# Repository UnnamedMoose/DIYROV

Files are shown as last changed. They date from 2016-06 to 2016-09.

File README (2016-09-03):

This is a README file for a home-made Remotely Operated Vehicle (ROV).
Please see Documentation/manual.pdf for detailed information about this project.

To start building your own ROV, simply checkout this repository and follow the instructions
in Documentation/manual.pdf. The individual folders of this repo contain:

- CAD - CAD files of the robot, including overview technical drawings in a pdf format.
	An Excel spreadsheet with basic design calculations is also provided. All of
	the CAD files are in Autodesk Inventor format, but an exchange file ROVassembly.stp
	has been included too. This may be imported into any CAD program (tested
	with SolidWorks 2015 Student Edition)
- Documentation - includes a report summarising the project and giving a description
	of how it all works. It gives instructions and practical tips on how to manufacture
	the ROV.
- Software
	+ controlInterface - contains Python files used to run the PC client that
		allows the ROV to be controlled
	+ HardwareInterfaces - includes custom Arduino libraries used to control
		various elements of functionality of the vehicle
	+ ROVMain - holds the main Arduino sketch that runs on the micro-controller
		on-board of the ROV
- BlockDiagrams - block diagrams of the ROV system and its various subsystem. These
	appear throughout Documentation/manual.pdf. The png versions of all the diagrams
	may be found in Documentation/Figures
- PCBDesigns - contains files used to produce PCB boards, organised in individual
	sub-folders (currently only motorControlBoard). Includes gerbers of the PCBs,
	which can readily be used to order the PCBs from a professional manufacturer
	or to etch them yourself.

Please see the LICENCE file for information on how this work may be used.

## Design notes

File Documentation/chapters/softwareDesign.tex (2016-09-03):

\pagestyle{chapter-fancy-style}
\chapter{Software design}

%=====================
\section{Overview}
The ROV software can be split into two distinct parts - the code present on the Arduino, which translates the operator commands to physical actions of the vehicle, as well as the shore-based computer part, which collects the user inputs and sends the corresponding commands to the Arduino. The remainder of this chapter covers both parts of the software separately. The computer part of the code is intended as cross-platform because its based on Python~2.7 and its open-source libraries. However, it has been developed and tested exclusively on Ubuntu 12 and 14.

%=====================
\section{Micro-controller}

%---------------------
\subsection{Program structure}
The Arduino only receives and executes operator commands, which means its functional flow is rather simple, as shown in the flowchart in Fig.~\ref{fig:arduinoMainLoop}. The \texttt{execute every instruction in series block} might involve arming the ESCs, sending readings of all the sensors, switching the forward LEDs on or off, and setting thrust levels and directions of all the motors.

\begin{figure}[]
\centering

\caption{Block diagram showing the flow of the Arduino \texttt{setup()} and \texttt{loop()} functions.}
\label{fig:arduinoMainLoop}
\end{figure}

%---------------------
\subsection{Hardware interfaces}
In order to interact with each piece of hardware, such as a sensor or electric motor, or in order to implement simple functionality, a special class \texttt{Module} has been implemented. This is holds fields such as \texttt{identifier} and \texttt{currentValue}, the combination of which is used to control a single aspect of the Arduino operation. For example, a~\texttt{Module} object called \texttt{refreshRate} holds the loop frequency the micro-controller operates at. Such basic objects typically get used directly in the \texttt{loop()} method and are treated as simple storage containers. For instance, at the end of each \texttt{loop()} call a new delay gets set as \texttt{delay(refreshRate.getValue());}, which allows setting the delay value using the same command protocol as used with more complex \texttt{Module}s.

Key methods of the \texttt{Module} class are the virtual \texttt{getValue()}, \texttt{setValue(int newValue)}, and \texttt{arm()} functions. Their default implementation in the \texttt{Module} class allows the user to read or set the value the object holds, for instance the refresh rate of the Arduino, or to initialise the object at the beginning of the execution.

Each of the modules gets created upon initialisation of the Arduino code and pointers to them are collected in arrays \texttt{Module* actuators[]} or \texttt{Module* sensors[]}, depending on their functionality. This arrangement allows the user to create classes derived from \texttt{Module} and overriding the functionality they execute when given or asked for a new value, at the same time allowing the same code in the main program loop to be used to interact with each object. A depiction of the currently used classes is shown in Figure \ref{fig:moduleClasses}. This approach is used primarily in the \texttt{parseInput()} method which is responsible for communication between the micro-controller and the PC or the \texttt{sendSensorReadings()} method which calls the \texttt{getValue()} function on each sensor module and encodes their readings into a string message which gets sent to the PC.

Currently implemented classes derived from \texttt{Module} are:
%
\begin{itemize}
\item \texttt{BrushlessDCMotor} - accepts negative and positive demand on the motor rps into the \texttt{setValue} function, treating negative values as reverse. Uses two assigned output pins in order to control the direction (binary digital output) and speed (PWM) of the motor via the ESC.
\item \texttt{LEDModule} - the value passed to the \texttt{setValue} method is treated as a binary switch telling the module to set the output pin either to HIGH or LOW state, thus controlling the LED.
\item \texttt{DepthSensor} - implements the \texttt{getValue()} method in order to return the current depth. Currently, this is a~\textbf{placeholder only}.
\end{itemize}

\begin{figure}[p]
\centering

\caption{Block diagram showing the class hierarchy of the \texttt{Module} classes used to control Arduino functionality.}
\label{fig:moduleClasses}
\end{figure}

%---------------------
\subsection{Communications}

The ROV communicates with the computer via a serial port using the USB connection. The process involves encoding messages into one-line strings and dumping them into the buffer for the other side to see. This imposes a need for strict formatting of the message packets, which is described in Table \ref{tab:commsEncoding}. Each message consists of a string flag denoting an action or a subsystem, for instance "forwardLED" or "sendSensorReadings", followed by an integer value. An arbitrary number of commands may be sent in any one packet although the length of the entire message is limited by the character buffer size on the Arduino.

During each loop, the micro-controller attempts to read data from the serial port. If any data is found, the \texttt{parseInput()} method gets called. This is responsible for checking whether the passed information conforms to the message encoding system. If yes, the string gets unwrapped into a series of flags and corresponding values. Certain flags do not require the value and so an arbitrary integer may be passed, typically a 1 indicating a boolean true.

Each flag is then compared to the names of the registered \texttt{Module} objects until a match has been found. The value corresponding to the flag gets then passed using the virtual \texttt{setValue(int value)}. This is implemented by each class derived from the baseline \texttt{Module} class if a special action is required when a new value gets passed. For instance, the \texttt{BrushlessDCMotor} class converts the integer throttle demand into values understood by the ESC and adjusts the PWM signal, flipping the thrust direction relay if necessary. Other modules holding simple integer or boolean values do not re-implement the \texttt{setValue} method.

\begin{table}[h]
\centering
\caption{Description of the special characters used to format string messages sent over the serial port.}
\label{tab:commsEncoding}
\begin{tabular}{@{}ll@{}}
\toprule
\textbf{Character} & \textbf{Meaning} \\ \midrule
$<$ & beginning of message to PC \\
$>$ & beginning of message to Arduino \\
, & delimiter \\
; & end of message \\
\bottomrule
\end{tabular}
\end{table}

%=====================
\section{Computer}

%---------------------
\subsection{Program structure}
The key piece of code that runs as an executable is the \texttt{ROVgui.py}. It
defines a class \texttt{rovGuiMainFrame}, which then gets executed inside~a 
wxWidgets application. The class itself is derived from a~base class, which
defines the basic functionality of the graphical user interface alone (discussed
in more detail later) but all of the code responsible for the operation of the
ROV itself is contained in \texttt{ROVgui.py}.
The class contains several timers which execute specific methods at fixed intervals,
for instance they ask the mirco-controller to send the sensor readings or pass
demands for the electric motors.
Each of the key aspects of the code will be discussed in more detail in the following
parts of this chapter.

%---------------------
\subsection{Communications}
The protocol used to communicate with the micro-controller via the serial connection
utilises the \texttt{serial} Python library. This simply opens a port and treats
it as a buffer to read and write from. All of the parsed messages adhere to the
structure used by the Arduino side, namely begin and end with specific characters
and each element is separated by a known delimiter. The following code listing
provides a minimum example showing how a known port is opened, written into and
read from.

\begin{lstlisting}[style=myPythonStyle,language=Python]
import serial
import time

BAUD_RATE = 19200
REFRESH_RATE = 100
PORT = "/dev/ttyACM0"

# open the connection
serialConnection = serial.Serial(PORT, BAUD_RATE, timeout = 2)

testMsgGood = True
try:
    serialConnection.inWaiting()
except:
    testMsgGood = False

if not serialConnection or not serialConnection.readable() or not testMsgGood:
    raise IOError("Connection is FUBAR!")

# keep looping and printing whatever we get from the serial
message = ">sendSensorReadings,1;"
while True:
	serialConnection.write(message)
    line = serialConnection.readline().replace("\n","")
    if line:
        print line
    time.sleep(1./REFRESH_RATE)
\end{lstlisting}

%---------------------
\subsection{User input}
Interface to the Xbox controller (Figure \ref{fig:xboxController}) has been
created using pyGame 1.9.1, an open-source library for game development.
The interface relies on pyGame joystick module capturing all the inputs provided
by the user via the controller as events. These are stored in a buffer and then
the main GUI function periodically calls the \texttt{parseEvents()} method implemented
in the \texttt{controller} class. This retrieves the most recent set of events,
clears the buffer, and updates the values of axes and button positions held
inside the \texttt{controller} object. From here they are accessed from the main GUI each time a new
set of input parameters gets sent to the micro-controller.
A minimum working example which captures the events and prings the current axes
positions in the terminal is provided

\begin{lstlisting}[style=myPythonStyle,language=Python]
import pygame
from pygame.locals import *

pygame.init()
clock = pygame.time.Clock()

joysticks = []
for i in range(0, pygame.joystick.get_count()):
        joysticks.append(pygame.joystick.Joystick(i))
        joysticks[-1].init()
        print "Detected joystick '",joysticks[-1].get_name(),"'"
while 1:
        clock.tick(60)
        for event in pygame.event.get():
                if event.type == QUIT:
                        print "Received event 'Quit', exiting."
                        return
                elif event.type == KEYDOWN and event.key == K_ESCAPE:
                        print "Escape key pressed, exiting."
                        return
                elif event.type == KEYDOWN:
                        print "Keydown,",event.key
                elif event.type == KEYUP:
                        print "Keyup,",event.key
                elif event.type == MOUSEMOTION:
                        print "Mouse movement detected."
                elif event.type == MOUSEBUTTONDOWN:
                        print "Mouse button",event.button,"down at",pygame.mouse.get_pos()
                elif event.type == MOUSEBUTTONUP:
                        print "Mouse button",event.button,"up at",pygame.mouse.get_pos()
                        
                elif event.type == JOYAXISMOTION:
                        print "Joystick '",joysticks[event.joy].get_name(),"' axis",event.axis,"motion."
                        if event.axis == 2:
                                print ' axis 2', event.value
                        elif event.axis == 5:
                                print ' axis 5', event.value
                elif event.type == JOYBUTTONDOWN:
                        print ("Joystick '",joysticks[event.joy].get_name(),
                            "' button",event.button,"down.")
                elif event.type == JOYBUTTONUP:
                        print "Joystick '",joysticks[event.joy].get_name(),"' button",event.button,"up."
                elif event.type == JOYHATMOTION:
                        print "Joystick '",joysticks[event.joy].get_name(),"' hat",event.hat," moved to",event.value
\end{lstlisting}

\begin{figure}[]
\begin{center}
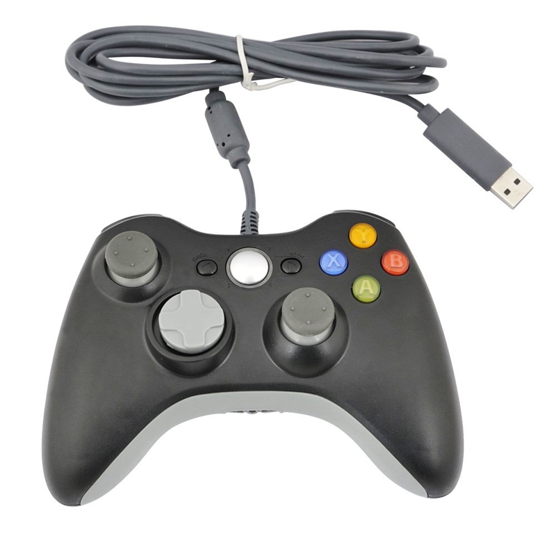
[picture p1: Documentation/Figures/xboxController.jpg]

\end{center}
\caption{USB Xbox controller used to provide control inputs to the ROV.}
\label{fig:xboxController}
\end{figure}

%---------------------
\subsection{Video acquisition}

In order to acquire imagery from the on-board USB camera, the code uses OpenCV 3.0.0-rc1,
a cross-platform, open-source digital imaging library. It is written in C++ but
provides a straightforward interface for use in Python.
In short, capturing a single frame is achieved as

\begin{lstlisting}[style=myPythonStyle,language=Python]
import cv2, wx
# create a camera
cameraID = 1
cameraCapture = cv2.VideoCapture(cameraID)
# get a picture and set up colours
ret, picture = cameraCapture.read()
height, width = picture.shape[:2]
picture = cv2.cvtColor(picture, cv2.COLOR_BGR2RGB)
# convert to wxWidgets bitmap for use inside the GUI
bmp = wx.BitmapFromBuffer(width, height, picture)
\end{lstlisting}

%---------------------
\subsection{Graphical interface}

Figure \ref{fig:GUI} shows the layout used to provide a graphical interface for
controlling the ROV. Live feed from the on-board camera is provided on the right-hand
side while the left is devoted to controlling the top-level functionality of the
vehicle. The top left-hand corner shows the thruster demand of each motor. Below,
controls are provided for the serial port connection to the Arduino, the video
feed of the camera, Xbox controller and arming of the electronic speed controllers
on board of the ROV.
There is also a pop-up Settings window which allows the user to adjust the
Arduino loop frequency, as well as frequencies for sending the control inputs,
receiving sensor readings, and camera frame rate.
The entire GUI runs on wxWidgets 2.8.12.1 and has been designed using wxFormBuilder,
both of which may be readily integrated with Python and are open-source.

\begin{figure}[]
\begin{center}
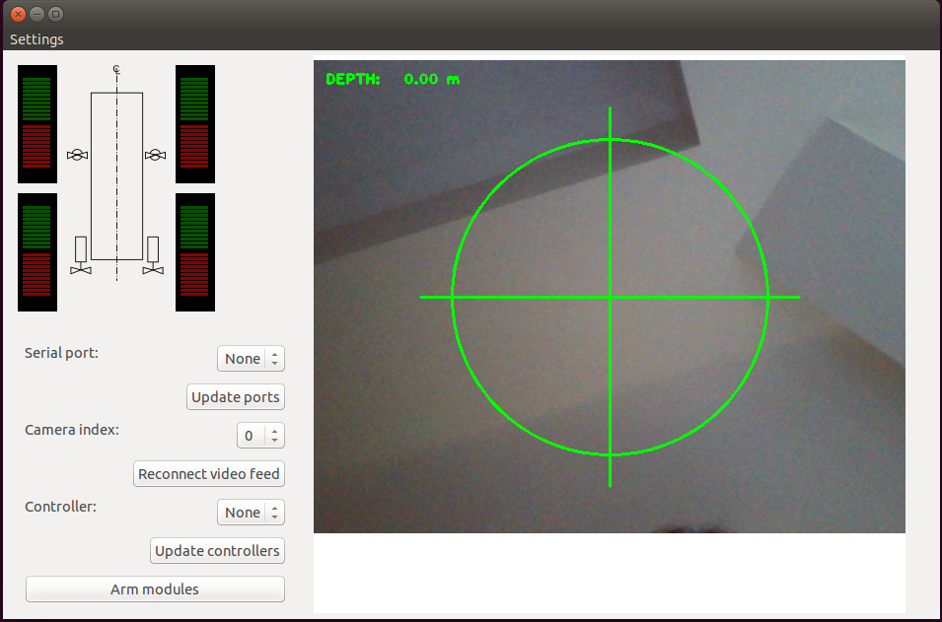
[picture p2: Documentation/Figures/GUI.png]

\end{center}
\caption{Graphical user interface (GUI) used to control the ROV from the laptop.}
\label{fig:GUI}
\end{figure}

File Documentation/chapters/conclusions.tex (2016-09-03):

\pagestyle{chapter-fancy-style}
\chapter{Conclusions}

%=====================
\section{Summary of the design}

It has been demonstrated that even within a~limited budged of less than £300 and
access only to basic tools, a~fully-functional remotely operated underwater vehicle 
can be designed, manufactured and tested.
The overall design concept using only four degrees of freedom control and employing
a compact vehicle shape has proven to provide sufficient performance that would be
expected of a low-cost sensor platform for use in shallow waters.
Several specific aspects of the design should be refined but a precious
few have also proven to be quite successful. Each of these groups will be discussed
in more detail in the subsequent parts of this chapter.

%=====================
\section{Successful design features}

Several of the chosen engineering solutions have been found to work particularly
well during the tests. These were:
%
\begin{itemize}
\item Using the on-board Arduino micro-controller to allow control of the ROV
	from a standard laptop has proven to be a very flexible and low-cost solution
\item The X-Box controller used to collect input data has been found to provide
	a robust, easy-to-use interface
\item Overall general arrangement of the vehicle has been successful and integrating
	all of the electronics into a removable internal frame allowed ease of access
	during assembly and disassembly
\item Placing the motors so that their thrust passes through the centre of gravity
	has allowed problem-free operation in the 4 DoF framework
\item Use of an external power source allowed the vehicle to be compact and
	lightweight, with the complete system fitting into an above-average sized
	rucksack and being easily transportable by hand.
\end{itemize}

%=====================
\section{Recommendations for future designs}

Despite the general success of the project, several aspects of the design could,
and a few certainly should, be improved if a next iteration or a brand new vehicle
were to be designed. These summarise the lessons learned through the development
and testing of the ROV:
%
\begin{itemize}
\item Making the aft plug removable without the use of bolts or other permanent
	connectors made it very easy to assemble the vehicle on-shore but led to
	the vehicle not being completely watertight. This is a major issue which
	could be addressed by i) using a threaded aft plug with a better seal
	ii) use of a slot-in plug secured with nuts and fitted with additional o-rings
	iii) manufacturing the pressure hull from a less compressible material (steel
	or aluminium) and desigining bespoke watertight connections
\item Removing pre-twist from the tether and making it float would make manoeuvring
	the vehicle far easier
\item Fixing the video latency issue would be necessary for operation in a real
	environment. This may require using a dedicated VGA cable, a different camera,
	or better implementation of the current software
\item At present the motors are placed in water without waterproofing which would not
	be acceptable in the long term in real environments such as seas or rivers.
	A watertight enclosure would be necessary, most likely utilising a magnetic
	coupling, to prevent corrosion of the motors.
\item Being able to redirect a time trace of control inputs and sensor readings to a file
	would make analysing the performance of the vehicle easier
\item In the present design only the internal structure was grounded, extending this
	to include all steel elements would add an important safety feature
\item Using non-linear mapping or having two sensitivity settings for the controller
	should make it easier to perform precise manoeuvres
\item Adding a sensor measuring power output of the battery would be an important
	indicator of the efficiency of the vehicle and would allow planning missions more accurately
\item At present, each of the power wires in the connector in the aft plug (section~\ref{ssection:connectorOnTheROV})
	ends with a~banana connector. Grouping the cables by the corresponding motors
	and using a~single connector for each motor
	would streamline the ROV assembly process significantly.
\item At present, the external steel frame is difficult to disassemble or even
	detach from the central hull due to the way the bolts are situated. At the
	time it was not considered crucial to allow this but having such a possibility
	would allow modifications to the design to be introduced more easily.
\item The electrical system has been significantly over-designed in most places
	in terms of current ratings. However, there are several segments with much lower
	safety factors, which effectively dictate the maximum safe power output from the battery.
	A~careful choice of suitable current ratings for each segment of the design would allow a~much
	more efficient overall system design.
\item Currently used off-the-shelf electronic speed controllers are straightforward
	to utilise but require a~large amount of wiring to operate, which takes up a~considerable
	amount of internal volume of the ROV. Using PCB-mounted variants or even controlling
	the motors directly from the Arduino by pulsing current using transistors could
	allow for a much more compact design. Ultimately, a~small PCB for a~single motor
	or a~pair of motors could be devised. The PCBs could be connected using stack-through
	connectors, thus eliminating most of the wiring used in the current design. This
	would make the system more modular, and lower-mass and thus also smaller and more agile.
\item Having the tether attach to the inspection hatch (aft plug) poses certain difficulties
	during disassembly as often multiple connectors have to be disconnected and reconnected
	just to allow a simple task to be accomplished. Moving the cable port to a stationary part
	of the hull could simplify these operations.
\item Adding controller calibration constants to the GUI settings window would make it more
	easily adjustable by the user.
\end{itemize}

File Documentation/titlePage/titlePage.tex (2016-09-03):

\begin{titlepage}

\newcommand{\HRule}{\rule{\linewidth}{0.5mm}} % Defines a new command for the horizontal lines, change thickness here

\center % Center everything on the page

%----------------------------------------------------------------------------------------
%	HEADING SECTIONS
%----------------------------------------------------------------------------------------
%\vspace*{-1cm}
%\hspace{8cm}\includegraphics[width=0.4\textwidth]{0_coreTemplate_UoSlogo_black.jpg}

\vspace*{1cm}
{\setstretch{1.5} % set bigger linespacing to make Capitals look better

%\textsc{\LARGE University of Southamtpon}\\[2.5cm] % Name of your university/college
\vspace{2.5cm}
\textsc{\huge DIY Remotely Operated Vehicle}\\[4.5cm] % Major heading

}
%----------------------------------------------------------------------------------------
%	TITLE SECTION
%----------------------------------------------------------------------------------------

\HRule \\[0.4cm]
{ \Huge \bfseries \documenttitle}\\[0.2cm] % Title of your document
\HRule \\[4.5cm]
 
%----------------------------------------------------------------------------------------
%	AUTHOR SECTION
%----------------------------------------------------------------------------------------

%\begin{minipage}{0.4\textwidth}
%\begin{flushleft} \Large
\begin{center}
\Large
\emph{Authors:}\\
Artur K. \textsc{Lidtke} \\
Aleksander A. \textsc{Lidtke}
\end{center}
%\end{flushleft}
%\end{minipage}
%~
%\begin{minipage}{0.4\textwidth}
%\begin{flushright} \Large
%\emph{Supervisors:} \\
%Prof. Stephen R. \textsc{Turnock} \\ % Supervisor's Name
%\end{flushright}
%\end{minipage}\\[4cm]

%----------------------------------------------------------------------------------------
%	DATE SECTION
%----------------------------------------------------------------------------------------

{\Large \today}\\[4cm] % Date, change the \today to a set date if you want to be precise

%----------------------------------------------------------------------------------------
%	LOGO SECTION
%----------------------------------------------------------------------------------------

%\includegraphics{Logo}\\[1cm] % Include a department/university logo - this will require the graphicx package
 
%----------------------------------------------------------------------------------------

\vfill % Fill the rest of the page with whitespace

\end{titlepage}

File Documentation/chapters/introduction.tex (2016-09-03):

\pagestyle{chapter-fancy-style}
\chapter{Introduction}

%=====================
\section{Aim}

The aim of this project was to develop a low-cost remotely operated underwater vehicle (ROV)
for operation in calm, shallow waters.
Its purpose was to allow principle physical and design challenges of building a robotic
underwater platform to be explored first-hand and to highlight possible future paths
for the development of a more refined design.
The intention of the project was not to deliver a state-of-the art vehicle and instead
focus was put on building experience and appreciation for the engineering challenges involved.
The ROV was to be manufactured, as much as possible, from easily available and affordable
off-the-shelf electronics and components. This would allow the devised solutions to
be easily reproducible by anyone with access to the most rudimentary tools and manufacturing
processes, making it easier to share the developed experiences.
The entire project, including software, CAD models, and design calculations is provided
on GitHub at \textcolor{blue}{\url{https://github.com/UnnamedMoose/DIYROV}}.

%=====================
\section{Objectives}

To achieve the specified aim, several objectives have been specified at the outset
of the project:

\begin{enumerate}
\item Create a simple software framework allowing basic electronic components to be controlled from
	a laptop via USB
\item Select a suitable means of propulsion for the ROV
\item Come up with a basic set of sensors which would make it easier to control the vehicle
	and provide basic feedback to the operator
\item Integrate the selected components into a coherent system and devise an arrangement that
	fits into a volume as small as possible
\item Design a watertight vessel to house the electronics using off-the-shelf, cheap DIY products
\item Assemble the ROV and test it in a calm environment such as a swimming pool or a~towing tank
\end{enumerate}

%=====================
\section{Subsequent parts of this document}

The following parts of this informal report will address each of the listed objectives,
and discuss them it in the context of the ultimate aim.
The intention is to convey both the engineering rationale and experience gained throughout the project,
rather than keeping the writing strictly technical. The report is accompanied by
the complete release of the necessary source code (both on-board microcontroller and shore-based computer),
CAD models of the ROV, and design calculations, all of which combined should allow
 the Reader to reproduce the process undertaken at their own leisure.

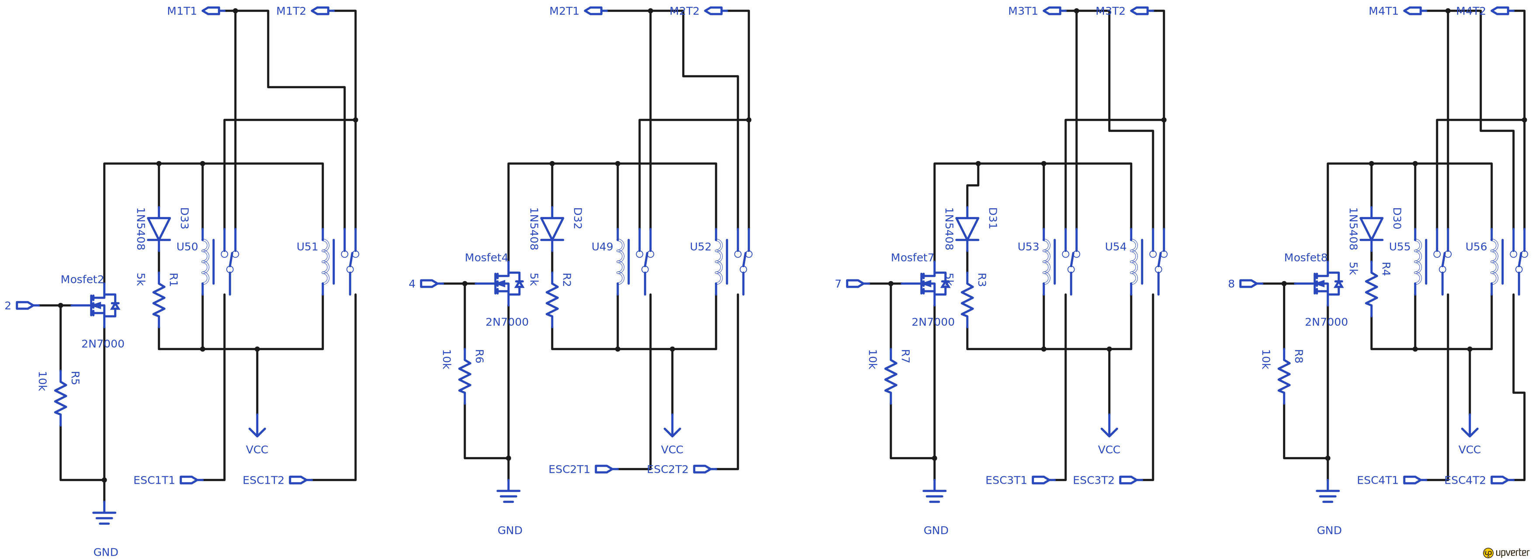
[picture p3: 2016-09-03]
PCBDesigns/BrushlessMotorControlBoard/BrushlessMotorControlBoard.png

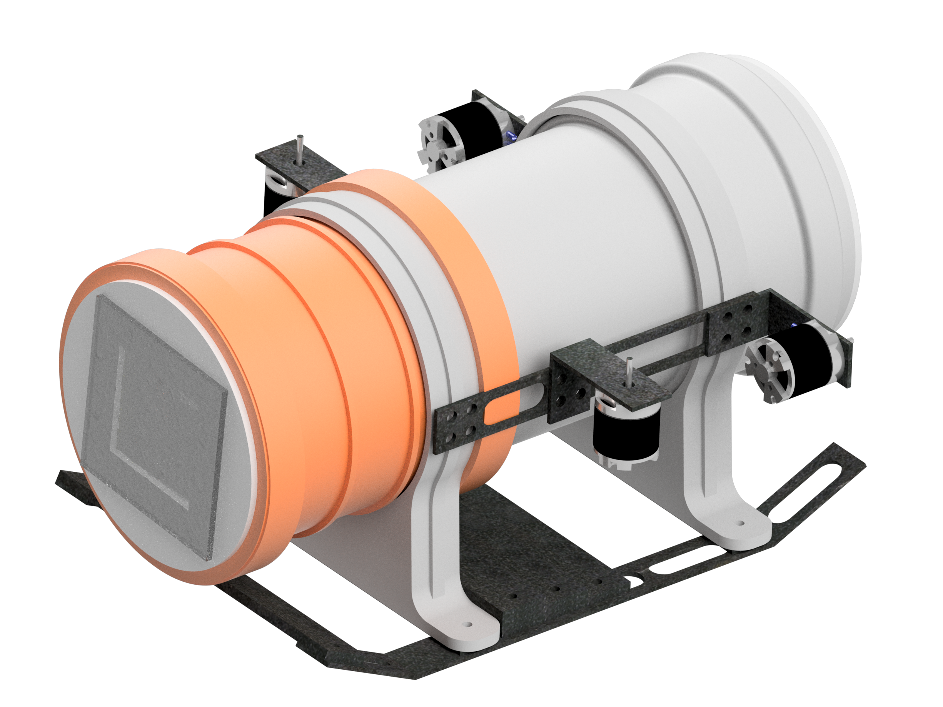
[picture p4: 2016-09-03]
Documentation/Figures/ROVrender0.png

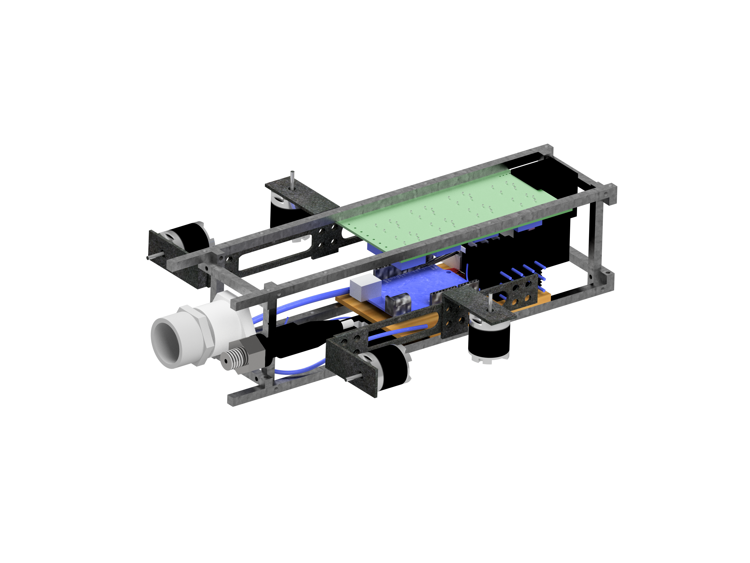
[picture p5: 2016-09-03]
Documentation/Figures/ROVrender1.png

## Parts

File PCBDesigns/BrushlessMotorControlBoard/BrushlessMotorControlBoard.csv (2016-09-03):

Reference Designator | Description | Manufacturer | Manufacturer Part Number | Suppliers | Package | Quantity | Verified Pin Names | Rms Reverse Voltage | Operating Temperature Range | Verified Pad Assignment | Verified Attributes | Average Rectified Output Current | Forward Voltage | Verified Geometry | Peak Repetitive Reverse Voltage | Mfg Package Ident | Footprint 0 Description | Imported From | Kind | Netlist | Code Jeita | Manufacturer Link | Code Jedec | Subkind | Packagedescription | Refdes | Resistance | Is Generic
D30 D31 D32 D33 | 3.0A SILICON RECTIFIER 1N5408 | Won-Top Electronics | 1N5408 |  | AXIAL | 4 | true | 700V | -65 to +125°C | true | true | 3.0A | 1.0V | true | 1000V | DO-201AD
Q1 | N-channel Enhancement Mode Field-effect Transistor | Fairchild | 2N7000 |  | TO92 | 1 | true |  |  | true | true |  |  | true |  |  | TO, Flat Index; 3 In-Line, Axial Leads; Body Dia. 4.6mm; Leads 0.48 x 0.45 mm (max) | Altium | General | @DESIGNATOR %1 %2 %3 @MODEL | SC-43 | http://www.semiconductors.philips.com/ | TO-92 | Spice Subcircuit | Plastic Single-Ended Leaded (through hole) package; 3 Leads (TO-92) | Mosfet2
Q5 | N-channel Enhancement Mode Field-effect Transistor | Fairchild | 2N7000 |  | TO92 | 1 | true |  |  | true | true |  |  | true |  |  | TO, Flat Index; 3 In-Line, Axial Leads; Body Dia. 4.6mm; Leads 0.48 x 0.45 mm (max) | Altium | General | @DESIGNATOR %1 %2 %3 @MODEL | SC-43 | http://www.semiconductors.philips.com/ | TO-92 | Spice Subcircuit | Plastic Single-Ended Leaded (through hole) package; 3 Leads (TO-92) | Mosfet4
Q6 | N-channel Enhancement Mode Field-effect Transistor | Fairchild | 2N7000 |  | TO92 | 1 | true |  |  | true | true |  |  | true |  |  | TO, Flat Index; 3 In-Line, Axial Leads; Body Dia. 4.6mm; Leads 0.48 x 0.45 mm (max) | Altium | General | @DESIGNATOR %1 %2 %3 @MODEL | SC-43 | http://www.semiconductors.philips.com/ | TO-92 | Spice Subcircuit | Plastic Single-Ended Leaded (through hole) package; 3 Leads (TO-92) | Mosfet7
Q7 | N-channel Enhancement Mode Field-effect Transistor | Fairchild | 2N7000 |  | TO92 | 1 | true |  |  | true | true |  |  | true |  |  | TO, Flat Index; 3 In-Line, Axial Leads; Body Dia. 4.6mm; Leads 0.48 x 0.45 mm (max) | Altium | General | @DESIGNATOR %1 %2 %3 @MODEL | SC-43 | http://www.semiconductors.philips.com/ | TO-92 | Spice Subcircuit | Plastic Single-Ended Leaded (through hole) package; 3 Leads (TO-92) | Mosfet8
R2 R3 R1 R4 | Generic Resistor (5k) | Generic | Resistor (5k) |  | Axial | 4 |  |  |  |  |  |  |  |  |  |  |  |  |  |  |  |  |  |  |  |  | 5k | true
R5 R6 R7 R8 | Generic Resistor (10000) | Generic | Resistor (10000) |  | Axial | 4 |  |  |  |  |  |  |  |  |  |  |  |  |  |  |  |  |  |  |  |  | 10000 | true
U49 U50 U51 U52 U53 U54 U55 U56 | Relay 5VDC | Songle Relay | JQC-3F-5VDC |  | PTH_RELAY | 8 | false |  |  | false | false |  |  | false

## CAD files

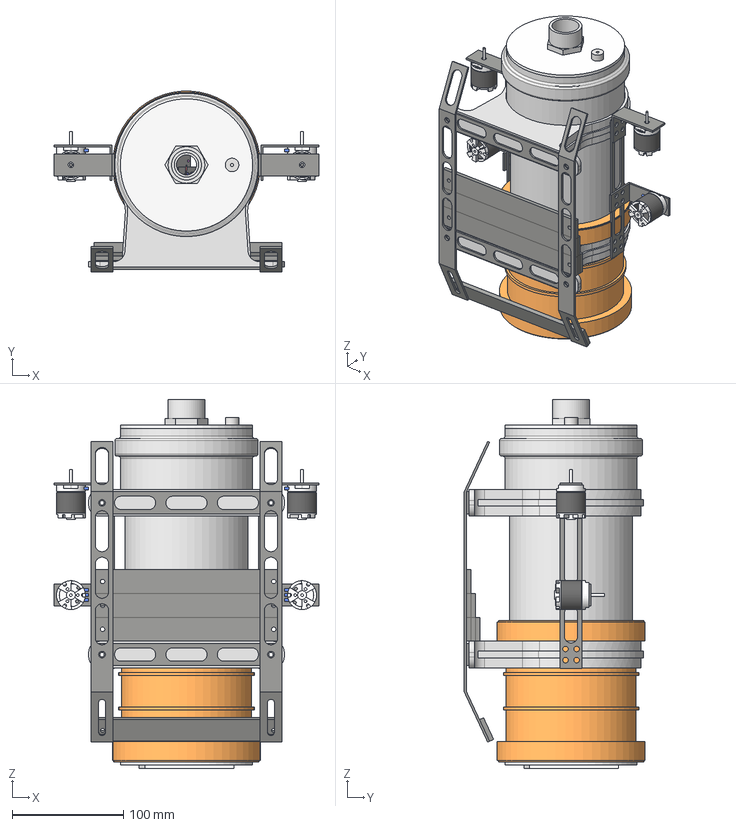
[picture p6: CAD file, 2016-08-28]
CAD/ROVassembly.stp
238.0 x 162.6 x 332.0 mm
hullPipe
longitudinal - bottom x 2
longitudinal - top x 2
transverse x 8
arduinoShelf
ArduinoUno
ESC x 4
usbRangeExtender
camera
Motor x 4
usbHubSmall
miniRelay x 8
aftPlug
PVCConnectorFemale3_4inch
frameMount x 7
plexiglassWindow
transverseClipStiffener x 2
sled x 2
30PSIPressureSensor
doubleSocketPipe
PVCConnectorMale3_4inch
socketBracket x 2
motorBracket x 4
brushlessMotorControlBoard
sideLongitudinal x 2
ROVassembly.ElectronicsHarness
CommonGNDVDD x 2
fwdPlug
ballastBarSmall
ballastBar x 6

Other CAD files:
CAD/30PSIPressureSensor.ipt
CAD/ArduinoUno.ipt
CAD/CommonGNDVDD.ipt
CAD/ESC.ipt
CAD/Motor.ipt
CAD/PVCConnectorFemale3_4inch.ipt
CAD/PVCConnectorMale3_4inch.ipt
CAD/ROVassembly.ElectronicsHarness.iam
CAD/ROVassembly.ElectronicsHarness.ipt
CAD/ROVassembly.iam
CAD/ROVassembly_external.idw
CAD/ROVassembly_internal.idw
CAD/aftPlug.ipt
CAD/arduinoShelf.ipt
CAD/ballastBar.ipt
CAD/ballastBarSmall.ipt
CAD/brushlessMotorControlBoard.ipt
CAD/camera.ipt
CAD/doubleSocketPipe.ipt
CAD/frameMount.ipt
CAD/fwdPlug.ipt
CAD/hullPipe.ipt
CAD/longitudinal - bottom.ipt
CAD/longitudinal - top.ipt
CAD/miniRelay.ipt
CAD/motorBracket.ipt
CAD/plexiglassWindow.ipt
CAD/sideLongitudinal.ipt
CAD/sled.ipt
CAD/socketBracket.ipt
CAD/transverse.ipt
CAD/transverseClipStiffener.ipt
CAD/usbHubSmall.ipt
CAD/usbRangeExtender.ipt

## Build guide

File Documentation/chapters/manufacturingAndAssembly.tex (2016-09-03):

\pagestyle{chapter-fancy-style}
\chapter{Manufacture and assembly}
%===============================================================================
\section{Architecture}
Overview of the ROV system is shown in Fig.~\ref{fig:systemBlockDiagram}, while Fig.~\ref{fig:rovGAsInternal} and Fig.~\ref{fig:rovGAsExternal} show the general dimensions of the vehicle and location of its major components. The ROV is based around an Arduino Uno R3, which is controlled and powered through its serial port connected to a~laptop. To overcome range limitations of ordinary USB cables, a~USB range extender is used, which transmits the USB signal and power over a~CAT5 cable.

The ROV houses one camera, which is operated over the same USB bus as the Arduino (the USB signal is split using an on-board USB hub). The camera field of view can be illuminated using three LED lights. Only one additional sensor, a~\unit[30]{PSI} pressure transducer, is present on board.

The ROV carries four \unit[750]{kV} brushless DC motors driven by four electronic speed controllers (ESCs). These enable forward/backward and up/down motion, as well as give control of yaw and roll. Preliminary study revealed that incorporating two additional motors, which would allow sideways motion, would require too big an investment. It would also increase the ROV displacement, thus making the vehicle larger than desired. The selected ESCs (chosen due to their low cost) can only provide thrust in one direction; a~custom printed circuit board (PCB) is used to reverse the thrust of individual motors.

The power to the motors is delivered from a~shore-based battery pack via a~three-wire power chord, which, together with the CAT5 cable, constitutes the ROV umbilical tether. The signals and power from the umbilical are delivered inside the pressure vessel via a~custom water-tight connector. In the current implementation, only the electronics sensitive to water are housed inside the pressure vessel while the brushless DC motors are exposed to water as shown in Fig.~\ref{fig:rovOverview}.

The final subsystem of the ROV, not shown in Fig.~\ref{fig:systemBlockDiagram}, is the external steel structure. It provides a~mounting point for the motors and ballast, as well as protects the ROV from hitting the bottom with the pressure vessel. The tether is also attached to this external structure, which can carry more load than the umbilical connector; this becomes important during emergency recovery, when the ROV is lifted out of the water by pulling on the tether.

The remainder of this chapter describes how the mentioned subsystems were manufactured, and how they are integrated into the system shown in Fig.~\ref{fig:systemBlockDiagram}. Components are grouped into subsystems based on their function. Thus, section~\ref{section:electronics} describes the electronics, which provide the ROV with its top-level functionality. The pressure vessel, made of PVC pipes and providing water-tight volume for the electronics, is described in section~\ref{section:pressureVessel}. The vessel is surrounded by an external structure described in section~\ref{section:externalStructure}. Lastly, the umbilical tether is described in section~\ref{section:umbilical}.

\begin{figure}[htb]
\begin{minipage}[b]{1\linewidth}
  \centering
	
\end{minipage}
\caption{The ROV system block diagram. \textcolor{cyan}{CAT5 cable} and \textcolor{red}{Three-wire power cord} constitute the umbilical tether (marked with the~pink rectangle). The black rectangle marks the extents of the pressure vessel.}
\label{fig:systemBlockDiagram}
\end{figure}

\begin{figure}[htb]
\begin{center}
	
\end{center}
\caption{External general arrangement of the current version of the ROV. Drawing not to scale, original provided in a~separate file.}
\label{fig:rovGAsExternal}
\end{figure}

\begin{figure}[htb]
\begin{center}
	
\end{center}
\caption{Internal general arrangement of the current version of the ROV. Drawing not to scale, original provided in a~separate file.}
\label{fig:rovGAsInternal}
\end{figure}

\begin{figure}[htb]
\begin{tabular}{c}
	\subfloat[CAD render]
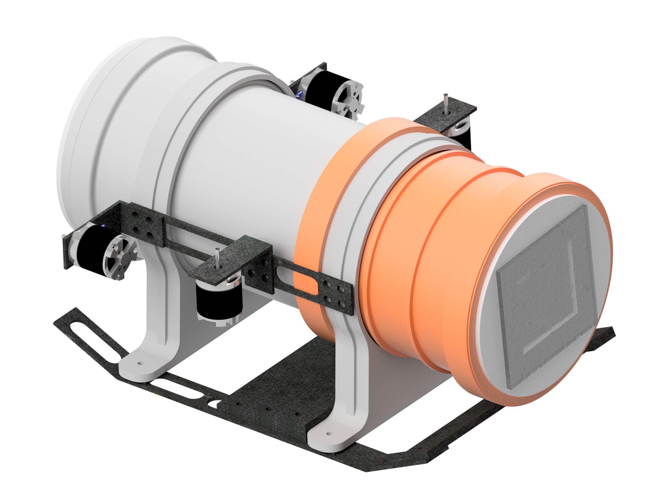
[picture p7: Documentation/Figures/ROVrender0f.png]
		{
		\label{fig:rovOverview:label:a} } \\
	\subfloat[Photo]
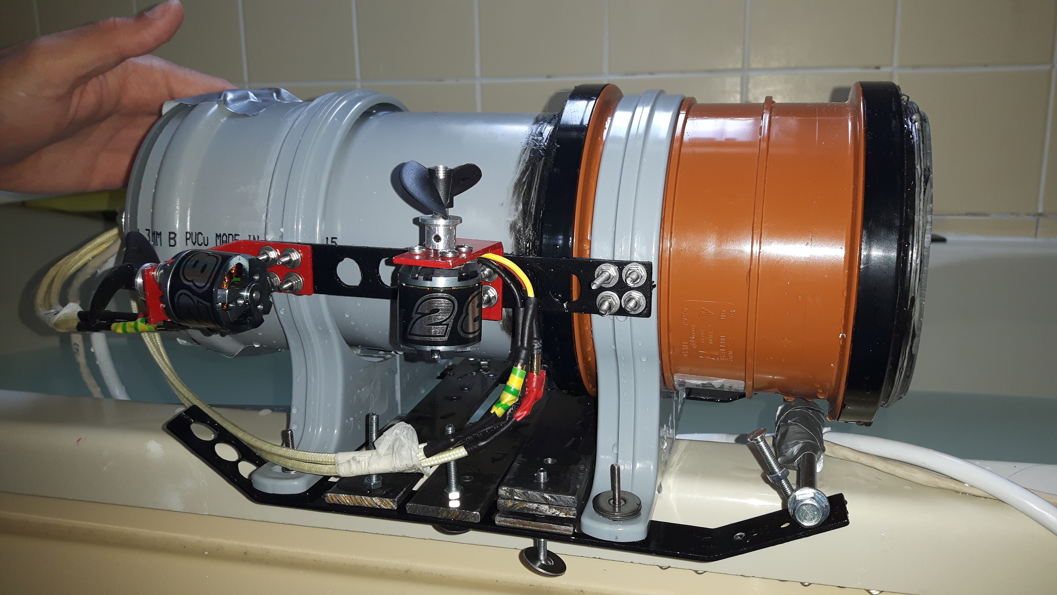
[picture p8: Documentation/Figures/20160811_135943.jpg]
		{
		\label{fig:rovOverview:label:b} } \\
\end{tabular}
\caption{Overview of the ROV.}
\label{fig:rovOverview}
\end{figure}

\clearpage % Avoid "too many unprocessed floats" error.

%===============================================================================
\section{On-board electronics}\label{section:electronics}

%-------------------------------------------------------------------------------
\subsection{Architecture and physical arrangement}
The electronics are mounted to an internal structure, which is made of \unit[4 by 4]{mm} aluminium bars. The bars are bolted together to form a~frame with a~square cross-section. The frame, with the electronics attached to it, slides into the pressure vessel as shown in Fig.~\ref{fig:electronicsSlideIn}. A~PVC plug (aft plug from section~\ref{sscetion:aftPlug}) then slides in and seals the pressure vessel. The electrical connections between the internal electronics, and the motors and the shore are routed through a~connector in the aft plug, described in section~\ref{ssection:connectorOnTheROV}.

The Arduino, USB hub and ESCs are mounted onto a~plywood bed, which bolts onto the aluminium frame. This plywood bed and the USB hub are visible in Fig.~\ref{fig:usbExtenderAndHub}. The PCB, which enables the thrust of the motors to be reversed (described in section~\ref{ssection:motorControlBoard}), is also bolted onto the frame, directly above the plywood bed as shown in Fig.~\ref{fig:simpleInternalOverview}. The camera is integrated into a~stand-alone module with three LEDs, as described in section~\ref{ssection:ledAndCamera}; this module is attached to the aluminium frame using cable ties. The USB range extender and power distribution units (described in section~\ref{ssection:powerDsitrbution}) are also attached to the internal frame using cable ties.

\begin{figure}[htb]
\begin{minipage}[b]{1\linewidth}
  \centering
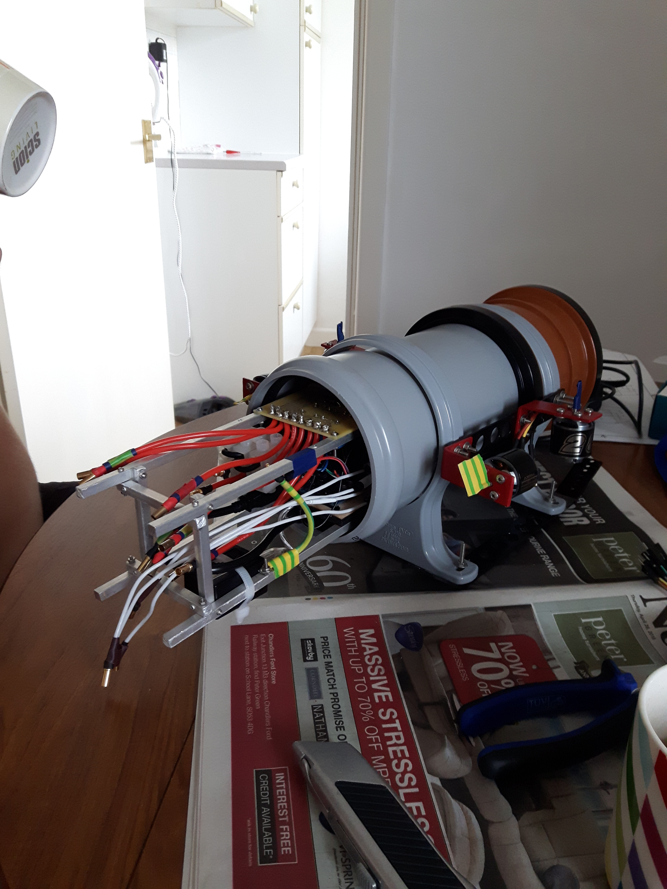
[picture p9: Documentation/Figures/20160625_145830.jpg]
	
\end{minipage}
\caption{Electronics are mounted to the internal aluminium structure, which slides into the pressure vessel.}
\label{fig:electronicsSlideIn}
\end{figure}

\begin{figure}[htb]
\begin{minipage}[b]{1\linewidth}
  \centering
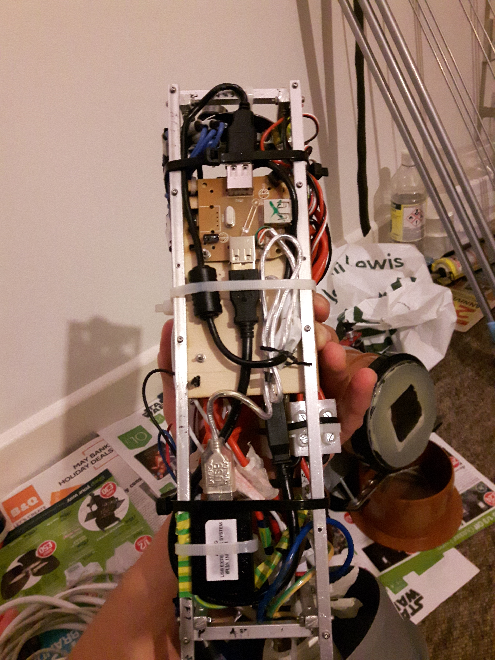
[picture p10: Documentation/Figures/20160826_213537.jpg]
	
\end{minipage}
\caption{USB range extender (black box on the bottom left of the phot) is mounted to the aluminium internal structure with a~white cable tie. The USB hub, into which Arduino and the webcam are plugged in, is bolted onto the underside of the plywood bed.}
\label{fig:usbExtenderAndHub}
\end{figure}

\begin{figure}[htb]
\begin{minipage}[b]{1\linewidth}
  \centering
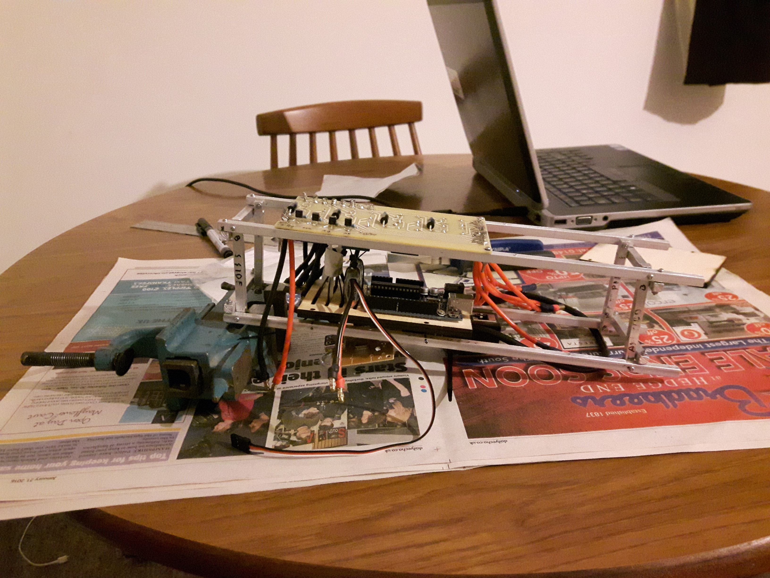
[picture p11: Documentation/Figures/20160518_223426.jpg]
	
\end{minipage}
\caption{General arrangement of the internal electronics. Only one electronic speed controller, and no LEDs and camera are mounted for clarity.}
\label{fig:simpleInternalOverview}
\end{figure}

\clearpage % Place these figures close to the text.

%-------------------------------------------------------------------------------
\subsection{Power distribution subsystem}\label{ssection:powerDsitrbution}
Block diagram of the on-board power distribution subsystem is shown in Fig.~\ref{fig:powerBlockDiagram}. The Arduino and the camera are powered directly from the USB bus delivered on board via the CAT5 cable, which forms part of the tether (c.f. section~\ref{section:umbilical}). The USB bus is changed from the CAT5 cable to a~standard USB cable using the USB range extender, and then split by the USB hub to deliver power to both the camera and the Arduino.

The pressure sensor is powered from the Arduino \unit[5]{V} pin. The LEDs are turned on by setting an Arduino pin high, which provides sufficient power for them to operate. Both the pressure sensor and the LEDs are connected to the Arduino ground, and connections to both peripherals are realised using hookup wires.

The power for the ESCs and the motor control board is delivered from the shore-based battery via the power cable, which constitutes part of the tether. Custom power distribution unit (PDU) and common ground for these five components were manufactured out of automotive cable connectors. These components are shown in Fig.~\ref{fig:commonGround}; they connect the ESCs and the motor control board in parallel.

The ground (GND) of the Arduino is connected to four ESCs. However, these connections are separate from the ones that deliver power to the ESCs (negative battery terminals). Whether the Arduino GND and and battery GND are connected via the ESCs is unknown. The motor control board connects the Arduino and battery GND, as described in section~\ref{ssection:motorControlBoard}.

Power is delivered to the ESCs and motor control board using gauge 32 wires (thick lines in Fig.~\ref{fig:powerBlockDiagram}). All other connections in Fig.~\ref{fig:powerBlockDiagram} are realised using hookup wires.

The third wire in the power cable (besides battery positive and negative terminals) is used to ground the internal structure. This is intended to protect the operators in case the battery positive terminal short-circuits to one of the internal components or the aluminium structure. The external structure is not grounded.

The shore battery pack constitutes two \unit[6]{V} batteries connected in series. These are housed inside an aluminium box, which also incorporates a~\unit[20]{mm} fuse, switches and leads that can be used to monitor the battery voltage. Disassembled battery pack is shown in Fig.~\ref{fig:batteryPack}.

\begin{figure}[htb]
\begin{minipage}[b]{1\linewidth}
  \centering
	
\end{minipage}
\caption{Block diagram of the power distribution subsystem. Power is delivered to the aft plug using the umbilical tether, which is connected to the battery pack.}
\label{fig:powerBlockDiagram}
\end{figure}

\begin{figure}[htb]
\begin{center}
\begin{tabular}{c c}
	\subfloat[Side]
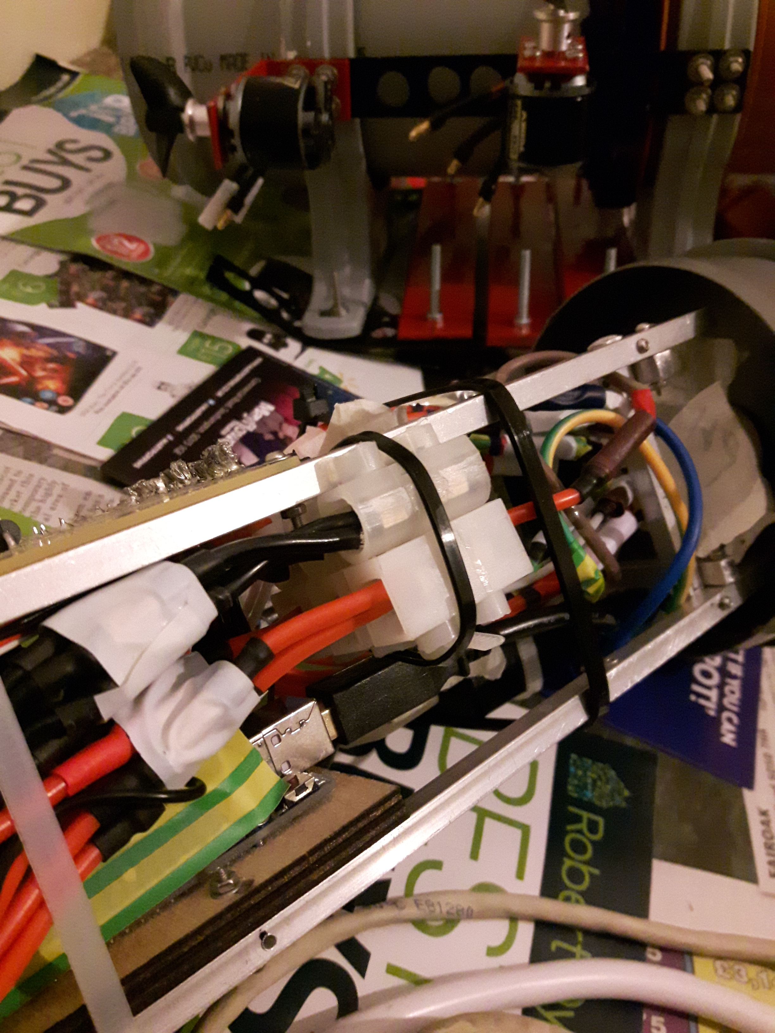
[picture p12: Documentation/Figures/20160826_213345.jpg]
		{
		\label{fig:commonGround:label:a} } &
	\subfloat[Top]
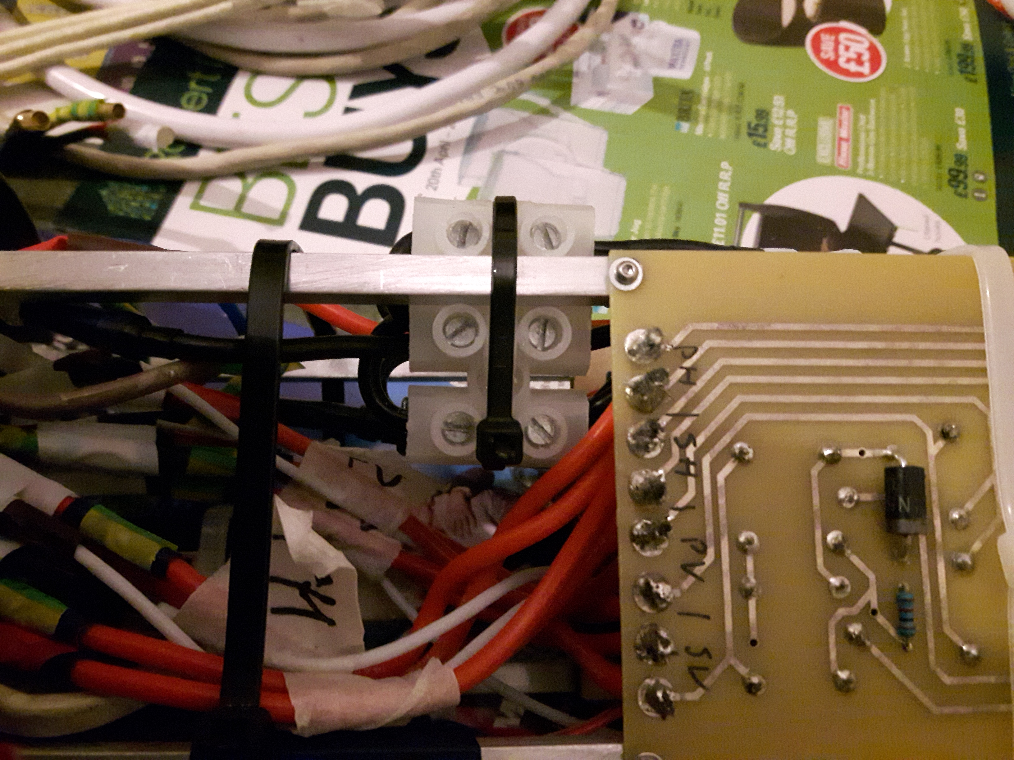
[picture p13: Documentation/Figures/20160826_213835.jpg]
		{
		\label{fig:commonGround:label:b} } \\
\end{tabular}
\end{center}
\caption{Side and top views of the common ground and common power lines made out of screw automotive cable connectors and mounted to the aluminium internal structure with cable ties.}
\label{fig:commonGround}
\end{figure}

\begin{figure}[htb]
\begin{minipage}[b]{1\linewidth}
  \centering
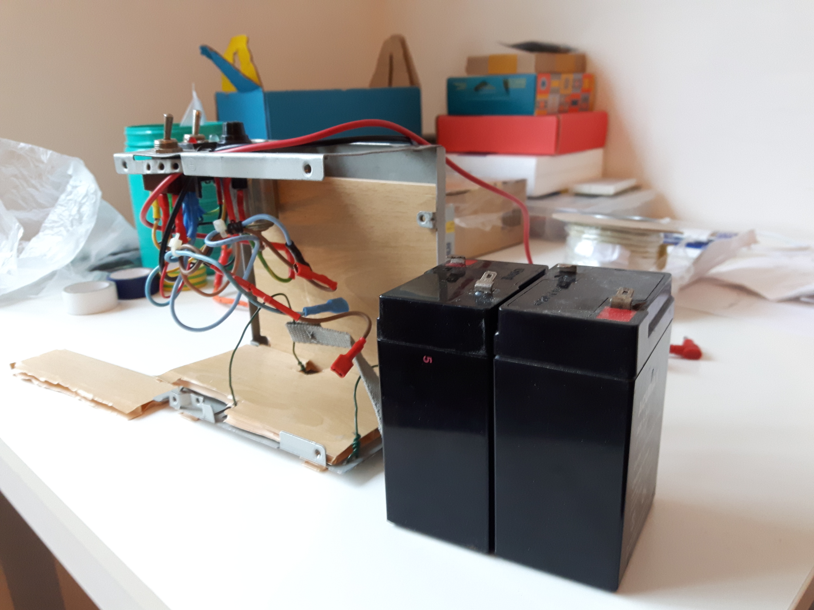
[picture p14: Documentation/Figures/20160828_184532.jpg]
	
\end{minipage}
\caption{Disassembled battery pack. One switch enables the batteries to be connected in parallel or in series (series configuration is used for the ROV project) while the other one switches the power on or off. The output of the battery pack is protected from excessive currents using a~\unit[20]{mm} fuse.}
\label{fig:batteryPack}
\end{figure}

\clearpage % Place these figures close to the text.

%-------------------------------------------------------------------------------
\subsection{Propulsion subsystem}\label{ssection:propulsionSubsystem}
Block diagram of the ROV propulsion subsystem is shown in Fig.~\ref{fig:propulsionBlockDiagram}. It is based on four brushless DC motors that are driven by four commercial, off-the-shelf electronic speed controllers. Every ESC converts a~pulse width modulation signal (PWM) from the Arduino into pulses of power delivered to every of three terminals on the brushless motor. Changing the frequency of the PWM changes the frequency of the power pulses, which changes the rotation frequency of the motor and so also its thrust. This PWM signal is delivered from the Arduino pins using hookup wires. The ESCs draw power, which is then delivered to the motors in pulses, directly from the shore-based batteries, which is described in section~\ref{ssection:powerDsitrbution}.

In order to reverse thrust of the motor, it suffices to swap two out of three signals output by the ESC. This is achieved by a~custom printed circuit board, which is described in more detail in section~\ref{ssection:motorControlBoard}. Two out of three outputs of every ESC (terminals 1 and 2 in Fig.~\ref{fig:propulsionBlockDiagram}) are routed through this board, before they are delivered to the corresponding motors using the connector in the aft plug using red wires in Fig.~\ref{fig:electronicsSlideIn}. The third signal of every ESC (terminal 3 in Fig.~\ref{fig:propulsionBlockDiagram}) circumvents the motor control board and connects to the corresponding motor only through the connector in the aft plug (white wires in Fig.~\ref{fig:electronicsSlideIn}). The commands to swap the thrust of a~given motor are issued to the motor control board via hookup wires connected to the Arduino pins.

The ESCs are mounted to the plywood bed ahead of the Arduino using cable ties (the aft-most ESC is visible in Fig.~\ref{fig:simpleInternalOverview}). The ESCs connect to the motor control board, the aft plug connector, and the motors using gauge 32 wires.

\begin{figure}[htb]
\begin{minipage}[b]{1\linewidth}
  \centering
	
\end{minipage}
\caption{Block diagram of the ROV propulsion subsystem. \textcolor{purple}{Connections from the Arduino} are realised using hookup wires. All other signals (\textcolor{red}{power}, and ESC signals \textcolor{green}{1, 2} and \textcolor{orange}{3}) are carried using gauge 32 wire.}
\label{fig:propulsionBlockDiagram}
\end{figure}

%-------------------------------------------------------------------------------
\subsection{Brushless-motor control board}\label{ssection:motorControlBoard}
As explained in section~\ref{ssection:propulsionSubsystem}, two signals from every ESC have to be swapped in order to reverse the thrust of a~motor. The schematic of the circuit, which achieves this, is shown in Fig.~\ref{fig:motorControlBoardSchematic}. Nominally, terminals 1 and 2 of every ESC (e.g. ESC1T1 and ESC1T2 for ESC no.~1) are connected to terminals 1 and 2 of the corresponding motor (e.g. M1T1 and M1T2 for motor no.~1). When a~command to reverse the thrust of a~given motor is issued by the Arduino by setting one of its pins high (e.g. pin~2 for motor no.~1), an n-type mosfet activates two switching relays. This connects terminals 1 and 2 of the ESC with terminals 2 and 1 of the motor, respectively, thus reversing the thrust. When the command pin is set low, the relays switch back to the nominal configuration and thrust is no longer reversed.

The power output of the Arduino is insufficient to activate the relays - relatively large relays, which can withstand currents output by the ESCs, have to be used. Thus, the power to the relays is delivered by the shore-based batteries. Every ESC-motor pair requires two switching relays, and every two relays have one flyback diode.

A~two-layer PCB houses the entire circuit from Fig.~\ref{fig:motorControlBoardSchematic}; its layout is shown in Fig.~\ref{fig:motorControlBoardLayout}. The motor control PCB is manufactured with 1 oz Cu and has trace widths of at least \unit[1]{mm} rated to at least \unit[2.5]{A}. The design of this board is open-source, and can be accessed in its repository at: \textcolor{blue}{\url{{www.upverter.com/AleksanderLidtke/7eccd1441d1097f8/BrushlessMotorControlBoard/}}}.

\begin{figure}[htb]
\begin{minipage}[b]{1\linewidth}
  \centering
	
\end{minipage}
\caption{Schematic of the brushless motor control PCB. The board connects terminals of ESCs to motor terminals via pairs of switching relays.}
\label{fig:motorControlBoardSchematic}
\end{figure}

\begin{figure}[htb]
\begin{minipage}[b]{1\linewidth}
  \centering
	
\end{minipage}
\caption{Layout of the brushless motor control PCB. Bottom copper marked with \textcolor{green}{green}, top with \textcolor{blue}{blue}, and component outlines with \textcolor{red}{red}. Switching relays are mounted on the top, and resistors, diodes and n-type mosfets on the bottom of the board. The PCB is actually mounted upside down in the vehicle, so that the bottom copper layer is facing the top of the ROV.}
\label{fig:motorControlBoardLayout}
\end{figure}

\clearpage % Place these figures close to the text.

%-------------------------------------------------------------------------------
\subsection{LEDs and camera}\label{ssection:ledAndCamera}
A~small, one-layer PCB, which houses three white LEDs connected in series, is mounted to a~reflective plastic surface. A~hole is drilled in the plastic, through which a~disassembled USB webcam is pointed in the direction of the LED lights. These LEDs and camera form a~stand-alone module, which is shown in Fig.~\ref{fig:forwardLED:label:a}. The module is mounted to the front of the internal aluminium frame of the ROV using cable ties, as shown in Fig.~\ref{fig:forwardLED:label:b}. A~translucent window is placed in the pressure vessel in front of the camera, which is described in section~\ref{ssection:forwardPlug}. As shown in Fig.~\ref{fig:powerBlockDiagram}, the LEDs are activated and powered directly from a~GPIO pin of the Arduino, whereas the camera is powered and operated via the USB bus.

\begin{figure}[htb]
\begin{center}
\begin{tabular}{c c}
	\subfloat[LED and camera module]
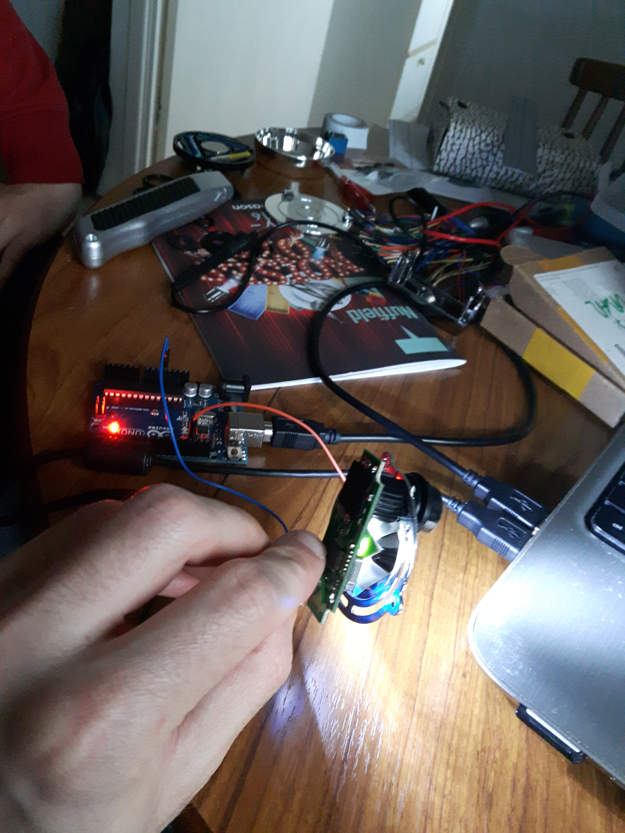
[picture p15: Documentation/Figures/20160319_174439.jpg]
		{
		\label{fig:forwardLED:label:a} } &
	\subfloat[Module mounting]
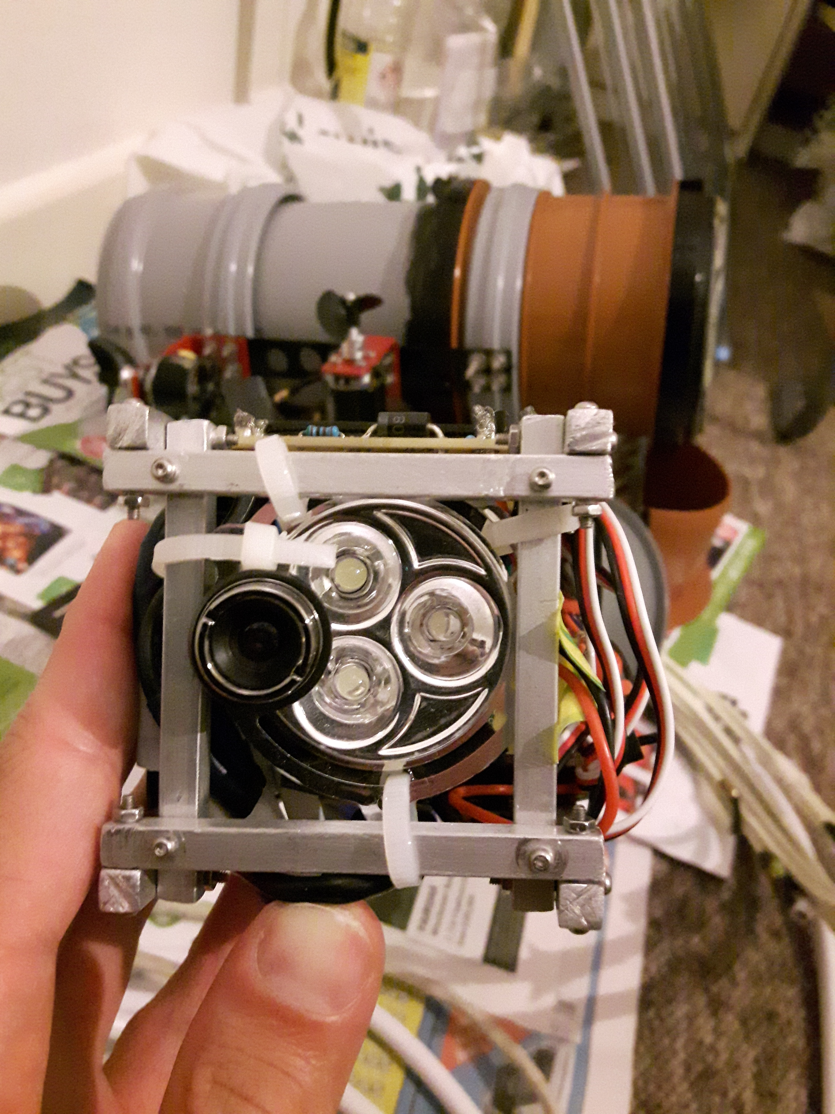
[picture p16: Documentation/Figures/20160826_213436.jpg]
		{
		\label{fig:forwardLED:label:b} } \\
\end{tabular}
\end{center}
\caption{The module, which houses the LEDs and the camera, and its mounting in the vehicle.}
\label{fig:forwardLED}
\end{figure}

%-------------------------------------------------------------------------------
\subsection{Pressure sensor}\label{ssection:pressureSensor}

A~\unit[30]{PSI} pressure transducer, depicted in Figure \ref{fig:pressureTransducer}, is mounted in the aft plug, which is a~modified PVC socket plug shown in Fig.~\ref{fig:socketPlug}. A~hole was punched in the socket plug, into which the pressure sensor was screwed in. The connection was sealed by applying PTFE tape on the thread of the pressure transducer and inserting rubber washers on either side of the socket plug. The entire assembly was then tightened using a~nut and a~washer placed on the external side of the socket plug. The inlet of the pressure sensor, brass nut and a~steel washer, under which a~rubber washer is placed, can be seen in Fig.~\ref{fig:externalSideOfTheAftPlug}. The transducer is powered from the Arduino \unit[5]{V} pin through a~hookup wire. It is connected to the Arduino GND and an analogue input pin using hookup wires as well.

\begin{figure}[htb]
\centering
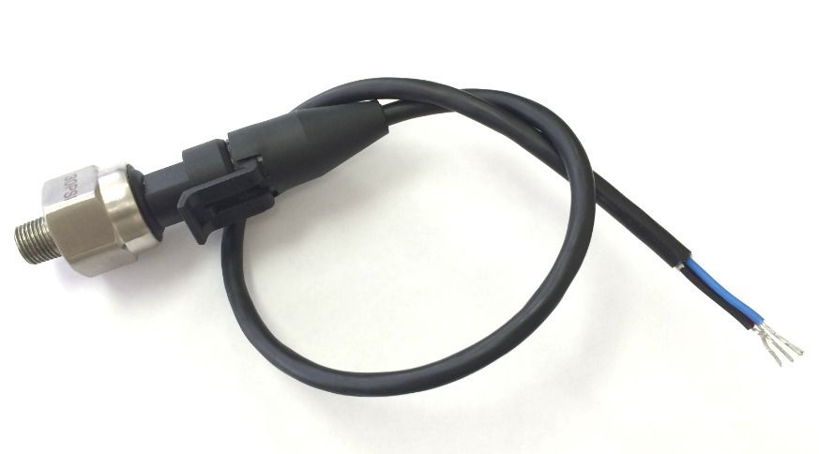
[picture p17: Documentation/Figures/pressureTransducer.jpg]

\caption{Overview of the pressure transducer.}
\label{fig:pressureTransducer}
\end{figure}

\begin{figure}[htb]
\begin{minipage}[b]{1\linewidth}
  \centering
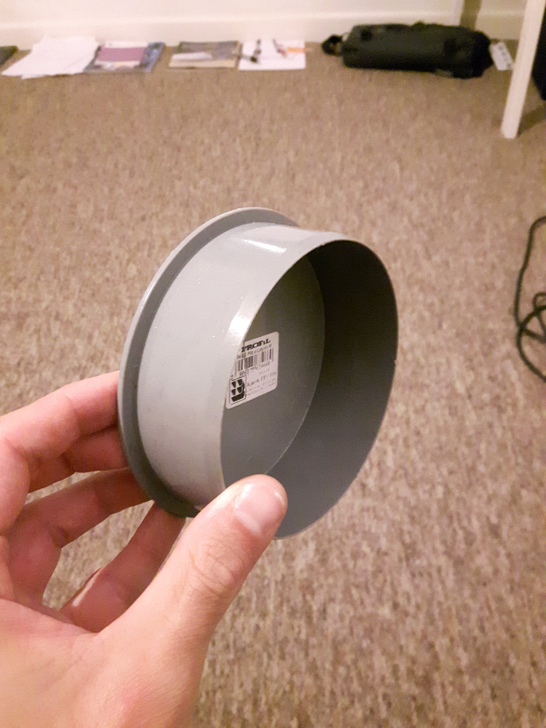
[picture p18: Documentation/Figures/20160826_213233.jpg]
	
\end{minipage}
\caption{Socket plug used to manufacture the aft and forward plug.}
\label{fig:socketPlug}
\end{figure}

%-------------------------------------------------------------------------------
\subsection{Ardunio pinout}\label{ssection:arduinoPinout}

Table \ref{tab:pinoutMain} describes all of the Arduino connections used by the ROV. Thrust direction pins are responsible for switching the relays on the motor control board via mosfet transistors, and throttle pins are connected to the ESCs directly and control motor rpm using PWM signals (see section~\ref{ssection:motorControlBoard} for details).

\begin{table}[h]
\centering
\caption{Pinout showing Arduino connections.}
\label{tab:pinoutMain}
\begin{tabular}{@{}ll@{}}
\toprule
\textbf{Pin  no.} & \textbf{Connect net} \\ \midrule
2 & Motor port horizontal - thrust direction \\
3 & Motor port horizontal - throttle \\
4 & Motor starboard horizontal - thrust direction \\
5 & Motor starboard horizontal - throttle \\
6 & Motor port vertical - throttle \\
7 & Motor port vertical - thrust direction \\
8 & Motor starboard vertical - thrust direction \\
9 & Motor starboard vertical - throttle \\
12 & Forward LED on/off \\
A0 & Pressure transducer analogue input \\
5 V & Pressure transducer VDD \\
\bottomrule
\end{tabular}
\end{table}

%===============================================================================
\section{Pressure vessel}\label{section:pressureVessel}

%-------------------------------------------------------------------------------
\subsection{Aft plug}\label{sscetion:aftPlug}
The aft plug is made of a~PVC socket plug shown in Fig.~\ref{fig:socketPlug}. Two holes were punched in it - one, into which the pressure transducer is screwed in, as described in section~\ref{ssection:pressureSensor}, and one, which houses the umbilical connector described in section~\ref{ssection:connectorOnTheROV}.

The external side of the aft plug (the wet side of the ROV), with the pressure transducer and umbilical connector mounted, is shown in Fig.~\ref{fig:externalSideOfTheAftPlug}. Its internal side is shown in Fig.~\ref{fig:internalSideOfTheAftPlug}; the body of the pressure sensor, CAT5 cable, power chord, and 12 motor wires (three signals per each of the four motors) can be seen on this side. The plug can be removed from the main pressure vessel to enable inspection and modification of the interior of the ROV. In order to ease the process and improve the water-tightness, silicone lubricant from Fig.~\ref{fig:lubricant} is applied on the aft plug before it is slid into the main pressure vessel. Once in place, the aft plug is secured using a~water-resistant duct tape.

\begin{figure}[htb]
\begin{minipage}[b]{1\linewidth}
  \centering
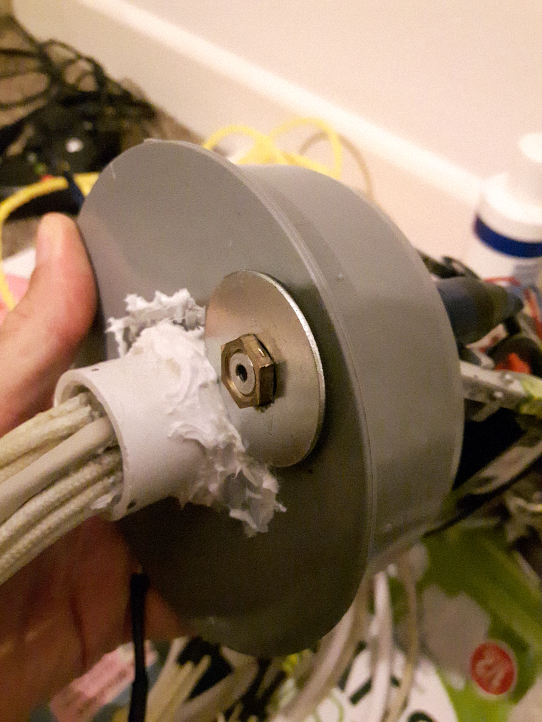
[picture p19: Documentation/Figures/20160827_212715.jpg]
	
\end{minipage}
\caption{External side of the aft plug with the pressure sensor and umbilical connector mounted.}
\label{fig:externalSideOfTheAftPlug}
\end{figure}

\begin{figure}[htb]
\begin{minipage}[b]{1\linewidth}
  \centering
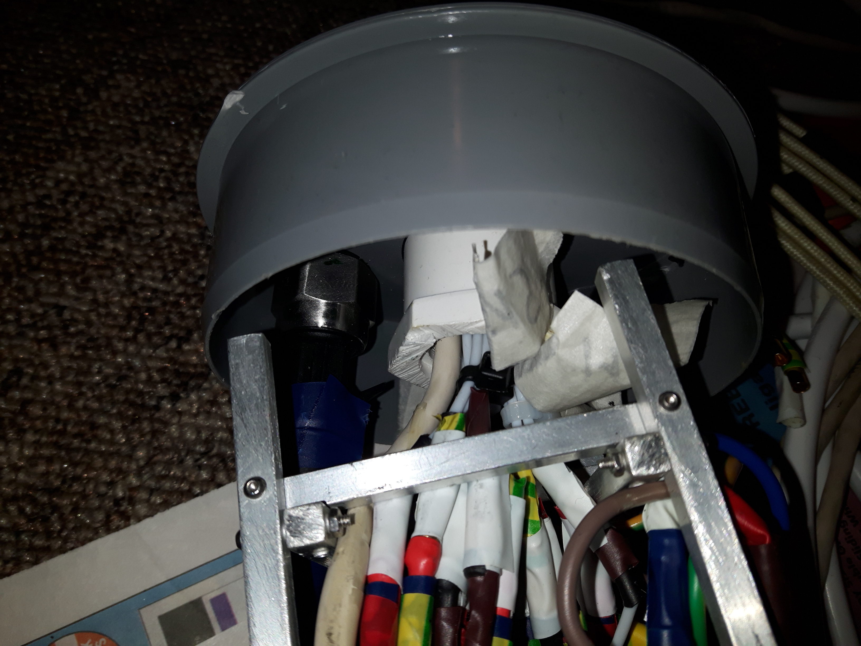
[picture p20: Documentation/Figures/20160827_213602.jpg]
	
\end{minipage}
\caption{Internal side of the aft plug with the pressure sensor and umbilical connectors mounted. The CAT5 cable is plugged into the USB range extender, and all motor wires are connected to the ESCs and the motor control board.}
\label{fig:internalSideOfTheAftPlug}
\end{figure}

\begin{figure}[htb]
\begin{minipage}[b]{1\linewidth}
  \centering
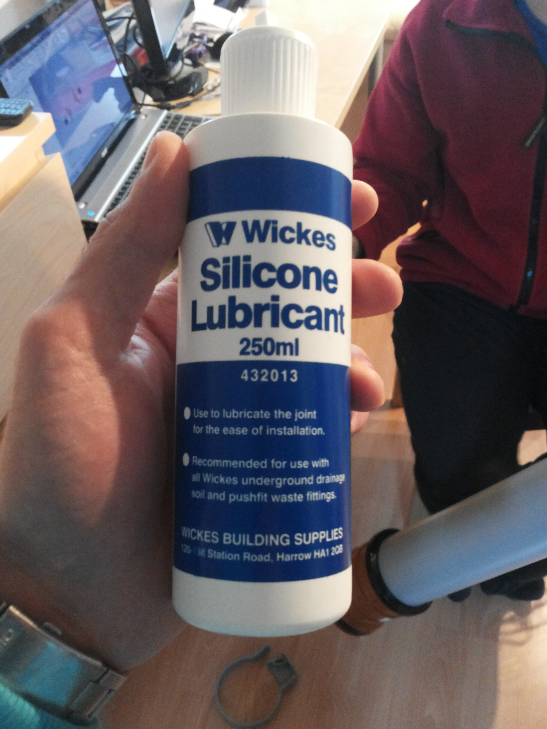
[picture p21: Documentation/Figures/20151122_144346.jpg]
	
\end{minipage}
\caption{When the aft plug is slid into the main pressure vessel, this silicone lubricant is applied onto it to ease the assembly and improve the seal.}
\label{fig:lubricant}
\end{figure}

%-------------------------------------------------------------------------------
\subsection{Forward plug}\label{ssection:forwardPlug}
The forward plug was manufactured from a~socket plug identical to the one used for manufacture of the aft plug (shown in Fig.~\ref{fig:socketPlug}). The forward plug has to enable the camera to photograph the space in front of the ROV to enable remote operation. To this end, a~hole was cut in the socket plug as shown in Fig.~\ref{fig:cuttingAHole}. A~window was cut out of a~\unit[4]{mm} thick plexiglass, which was glued onto the outer side of the socket plug using a~two-part epoxy glue. The complete forward plug is fixed in the pressure vessel using silicone; this provides both structural strength and makes the connection water-tight. The complete forward plug, mounted into the pressure vessel, can be seen in Fig.~\ref{fig:assembledPressureVessel}.

\begin{figure}[htb]
\begin{minipage}[b]{1\linewidth}
  \centering
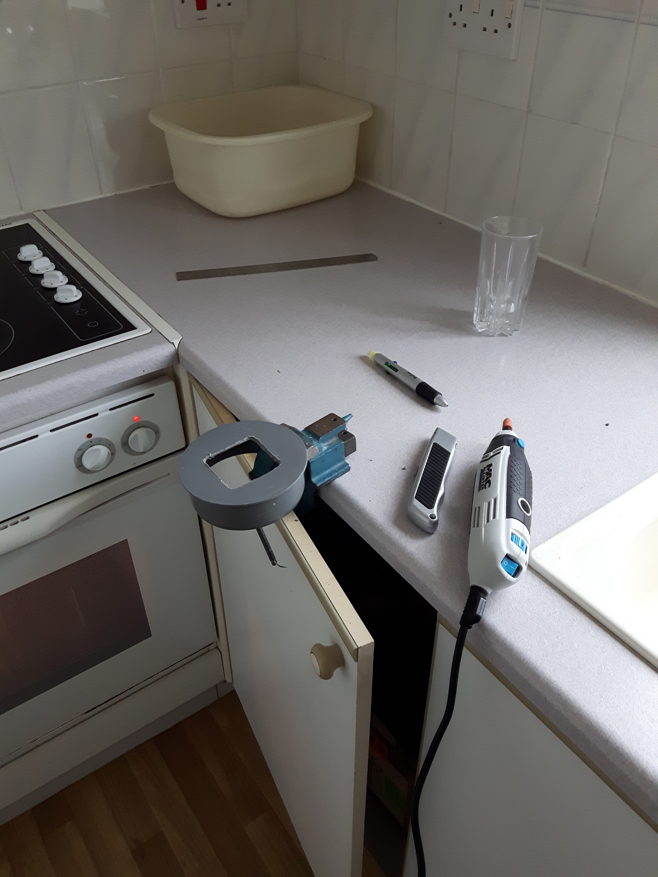
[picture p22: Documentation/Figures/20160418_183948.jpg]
	
\end{minipage}
\caption{Cutting a~hole in the socket plug to provide a~viewing window for the camera.}
\label{fig:cuttingAHole}
\end{figure}

%-------------------------------------------------------------------------------
\subsection{Main vessel}
The main pressure vessel is made of two PVC pipes, shown in Fig.~\ref{fig:pressureVesselPipes}. The orange double-sided socket is located on the bow of the ROV. The grey socket pipe was cut to the right length (to provide sufficient displacement), slid into the orange double socket, and secured using silicone. This connection is water-tight, and provides structural rigidity and strength. The assembled pressure vessel is shown in Fig.~\ref{fig:assembledPressureVessel}.

Apparently, PVC pipes of the same dimensions can have different masses, depending on their manufacturer. The ones used for this ROV were bought at Wickes, a~UK DIY supermarket.

\begin{figure}[htb]
\begin{minipage}[b]{1\linewidth}
  \centering
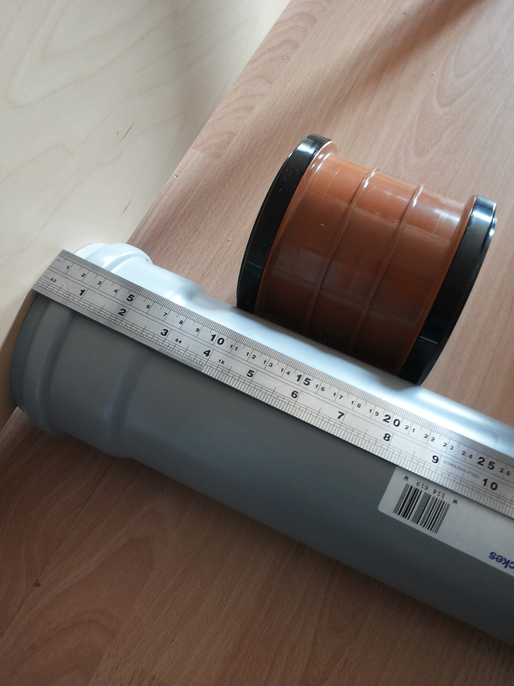
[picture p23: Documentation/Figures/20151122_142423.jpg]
	
\end{minipage}
\caption{The pressure vessel consists of two main parts - an orange double-sided socket and a~grey socket pipe.}
\label{fig:pressureVesselPipes}
\end{figure}

\begin{figure}[htb]
\begin{minipage}[b]{1\linewidth}
  \centering
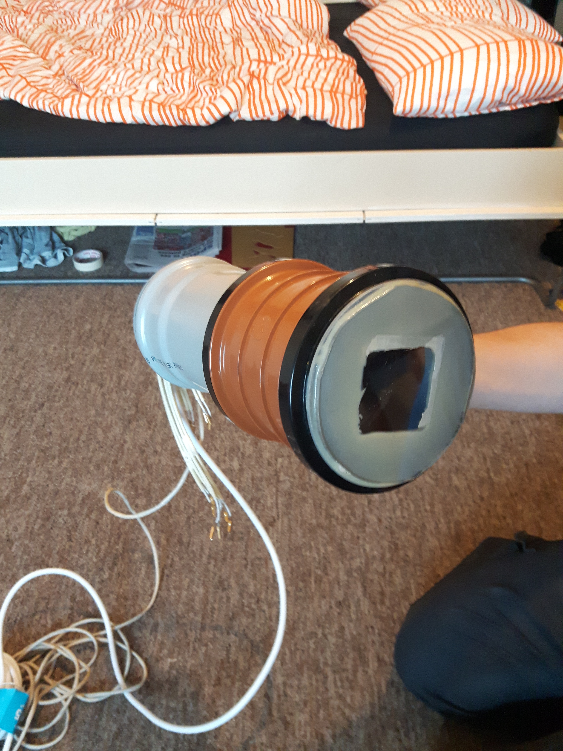
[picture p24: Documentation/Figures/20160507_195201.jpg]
	
\end{minipage}
\caption{Assembled pressure vessel.}
\label{fig:assembledPressureVessel}
\end{figure}

\clearpage % Avoid "too many unprocessed floats" error.

%===============================================================================
\section{External structure}\label{section:externalStructure}
For the naming convention and location of the components of the external structure, please refer to Fig.~\ref{fig:rovGAsExternal}.

%-------------------------------------------------------------------------------
\subsection{Transversals and longitudinals}
Side longitudinals, trasnverse clip stiffeners, and landing sleds were made of \unit[2]{mm} thick, \unit[20]{mm} wide rolled steel. In order to reduce their mass, M10 holes were drilled along their lengths. The structure is bolted together using M3 bolts. All the metal parts are painted to reduce corrosion.

%-------------------------------------------------------------------------------
\subsection{Pressure vessel mounting}
In order to mate the external metal structure with the pressure vessel made of PVC pipes, PVC socket brackets are used. The landing sleds and transversal clip stiffeners are bolted onto the default mounting holes in the brackets, which can be seen on the bottom of Fig.~\ref{fig:motorMountingDetails:label:a}. In order to mount the side longitudinals and motors, additional M3 holes were drilled in the socket brackets, as shown in Fig.~\ref{fig:brackets} and Fig.~\ref{fig:motorMountingDetails:label:a}.

The steel structure was bolted together and onto the socket brackets, but one side of every bracket was left free (one bolt going through the landing sled and transverse clip stiffener was not inserted). Then, the pressure vessel was inserted into the brackets, and the loose end of every bracket was fixed in place around the pressure vessel by bolting it onto the sled and the transverse clip stiffener.

To prevent the steel structure from slipping along the pressure vessel, the bow bracket was placed in the groove in the double socket pipe, as shown in Fig.~\ref{fig:brackets}. To stop the brackets from rotating around the pressure vessel, both of them were glued to it using a~two-part epoxy glue.

\begin{figure}[htb]
\begin{minipage}[b]{1\linewidth}
  \centering
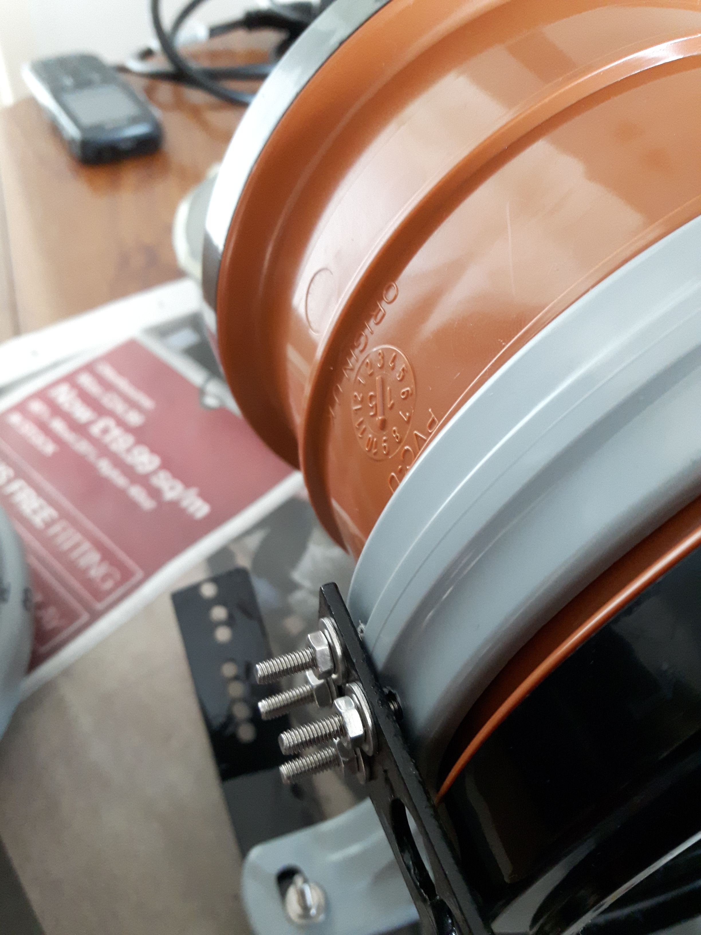
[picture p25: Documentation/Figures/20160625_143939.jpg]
	
\end{minipage}
\caption{Using socket brackets to mount the steel structure onto the pressure vessel. One of the brackets is placed in the grooves in the double-socket pipe to stop them from slipping along the ROV.}
\label{fig:brackets}
\end{figure}

%-------------------------------------------------------------------------------
\subsection{Motor mounting}
Motors are bolted onto custom brackets made of bent steel (\unit[2 by 20]{mm} section) using M2.5 bolts. The motor manufacturer does not provide a~detailed drawing that specifies the location of the mounting holes. Therefore, the location of the holes was marked on the brackets by using the motors themselves as a~guide. To ensure that the motors rotate freely, they are separated from their brackets using two washers, as shown in Fig.~\ref{fig:motorMountingDetails:label:b}.

The vertical motor brackets are located in the approximate longitudinal centre of buoyancy (centre of the pressure vessel) to reduce the pitching moment that the vertical motors impart on the vehicle. Similarly, the horizontal motor brackets are mounted at the vertical centre of buoyancy. To reduce the number of the holes in the socket brackets, both sets of motor brackets are bolted onto the side longitudinals, which are then bolted onto the socket brackets, as shown in Fig.~\ref{fig:motorMountingDetails}.

\begin{figure}[htb]
\begin{center}
\begin{tabular}{c c}
	\subfloat[Back]
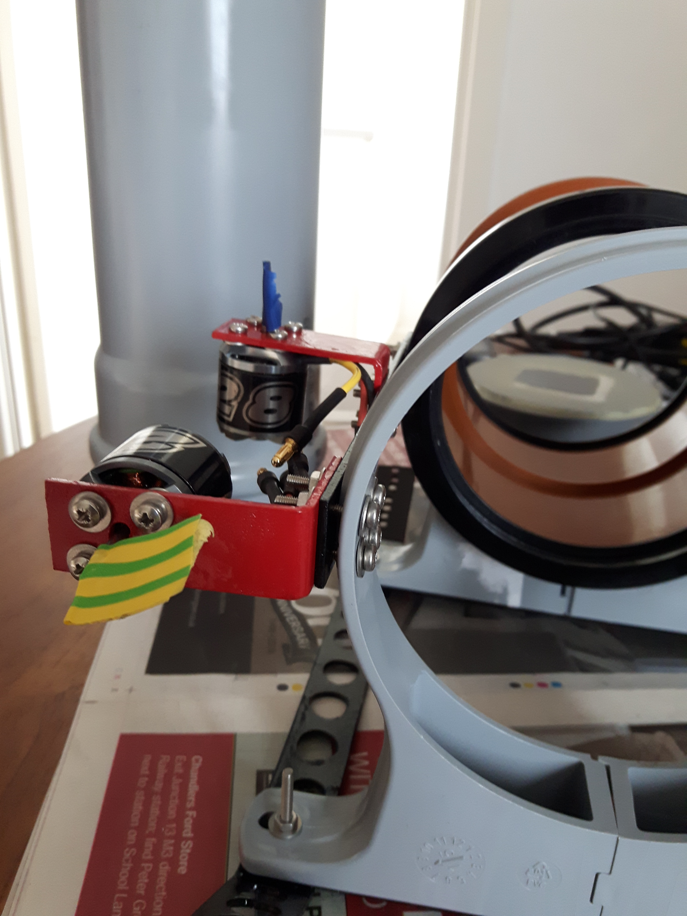
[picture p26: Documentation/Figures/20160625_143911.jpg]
		{
		\label{fig:motorMountingDetails:label:a} } &
	\subfloat[Top]
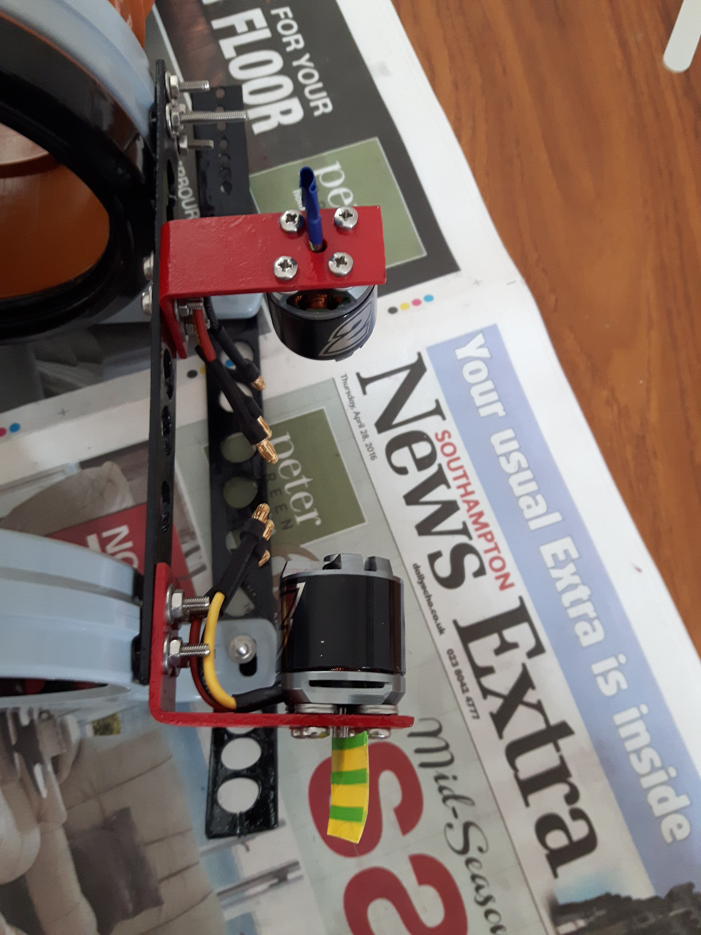
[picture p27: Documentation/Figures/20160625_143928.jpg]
		{
		\label{fig:motorMountingDetails:label:b} } \\
\end{tabular}
\end{center}
\caption{Details of mounting the motors onto the external steel structure. Views from the top and back of the vehicle.}
\label{fig:motorMountingDetails}
\end{figure}

%-------------------------------------------------------------------------------
\subsection{Ballast}
The ballast consists of two sets of elements: \unit[4 by 30]{mm} rolled steel flat-bar section cut to the length of the transverse clip stiffeners, and a~\unit[186]{mm} long, \unit[2 by 20]{mm} steel bar. The latter was a~left-over from the steel bought to manufacture the external frame.

Five of the \unit[4 by 30]{mm} sections are mounted close to the centre of gravity in order to compensate for the excess net buoyancy available from the hull. They are placed slightly forward to balance out the moment generated by the heavy wires and cables placed at the aft end. The smaller ballast bar is placed at the forward end of the sled and its exact position was adjusted to achieve an even trim. This was possible thanks to there being a~series of holes on either side of the sled, which allow fine-tuning of the ballast position. The arrangement of the ballast is indicated in Fig.~\ref{fig:rovGAsExternal}.

\clearpage % Avoid "too many unprocessed floats" error.

%===============================================================================
\section{Umbilical}\label{section:umbilical}

%-------------------------------------------------------------------------------
\subsection{Connector on the ROV}\label{ssection:connectorOnTheROV}
The connector enables the CAT5 cable and the shore power cable, which form the tether described in more detail in section~\ref{ssection:tether}, as well as the wires carrying signals from the ESCs to the motors described in section~\ref{ssection:propulsionSubsystem}, to penetrate inside the pressure vessel without compromising water tightness.

The connector is based on a~threaded PVC connector, the male part of which is shown in Fig.~\ref{fig:pvcConnector}. All the mentioned cables and wires were threaded through the male connector, which was then filled with a~two-part epoxy resin. All the wires were stripped out of their outermost covers as shown in Fig.~\ref{fig:strippingWires} to allow the resin to penetrate as deep into the wires as possible, to reduce the possibility of water dripping into the pressure vessel between the resin and the wires' cores. For the same reasons, the wires were separated from each other when applying the epoxy, as shown in Fig.~\ref{fig:separatingTheWires}. This ensured that some resin was present between all the wires.

Once complete, the male connector with wires laminated-in was screwed into the hole punched in the aft plug from its outer side, with PTFE tape used to seal the thread. Two rubber washers were placed on the connector, on both the inner and outer sides of the aft plug. A~complementary, female part of the PVC connector was then screwed onto the male counterpart to remove the voids between the washers and the PVC parts. Lastly, silicone was applied to the outer side of the aft plug to further seal the connector. The complete aft plug, with the connector screwed in and silicone applied, is shown in Fig.~\ref{fig:externalSideOfTheAftPlug}.

Banana connectors were soldered onto the motor wires. The motor wires were then connected to the motors, and the ESCs and the motor control board (described in section~\ref{ssection:propulsionSubsystem}) such that forward and upward thrust would be produced without the relays on the motor control board being activated. The wires were colour-coded to ease re-assembly in this configuration. Finally, after the final assembly, the wires were fixed using white electrical tape, which also isolates the banana connectors from each other. The colour coding of the motor wires and the white electrical tape can be seen in Fig.~\ref{fig:internalSideOfTheAftPlug}.

\begin{figure}[htb]
\begin{minipage}[b]{1\linewidth}
  \centering
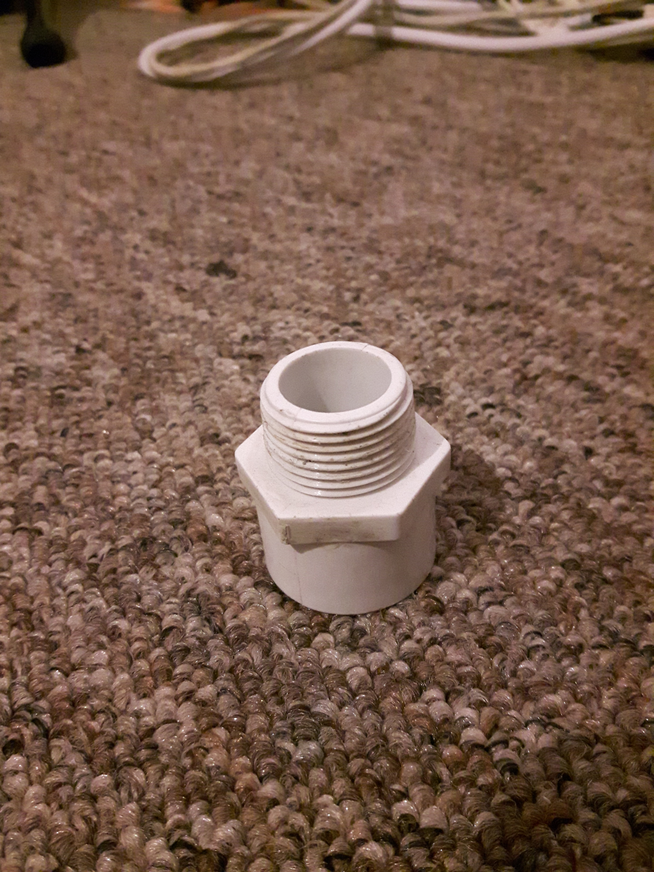
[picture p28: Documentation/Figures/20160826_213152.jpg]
	
\end{minipage}
\caption{Male part of the PVC connector through which the umbilical tether is threaded and then laminated.}
\label{fig:pvcConnector}
\end{figure}

\begin{figure}[htb]
\begin{center}
\begin{tabular}{c}
	\subfloat[Motor wires]
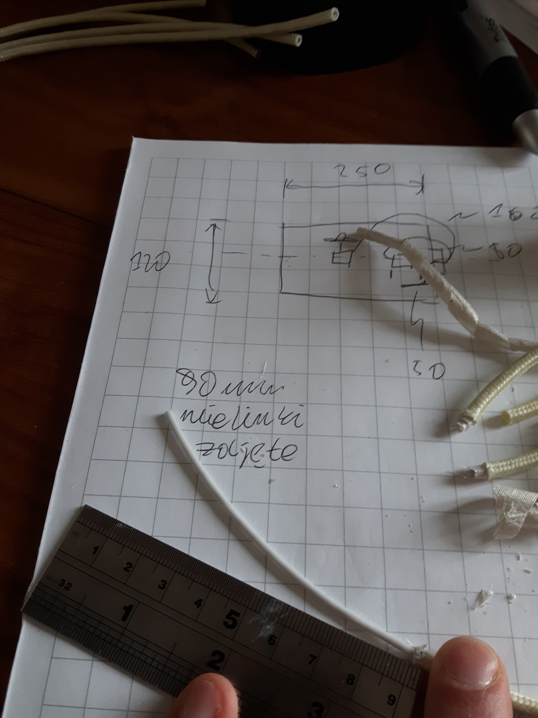
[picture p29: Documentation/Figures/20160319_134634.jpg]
		{
		\label{fig:strippingWires:label:a} } \\
	\subfloat[CAT5 cable]
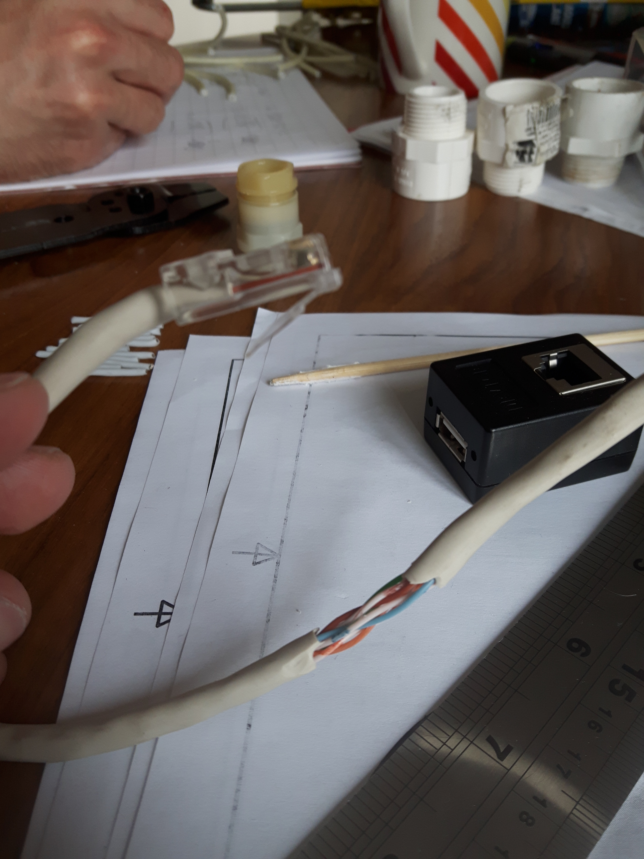
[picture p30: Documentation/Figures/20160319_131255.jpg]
		{
		\label{fig:strippingWires:label:b} } \\
\end{tabular}
\end{center}
\caption{External cover of the wires is stripped so that less water drips through the umbilical connector once the wires are laminated in place.}
\label{fig:strippingWires}
\end{figure}

\begin{figure}[htb]
\begin{center}
\begin{tabular}{c c}
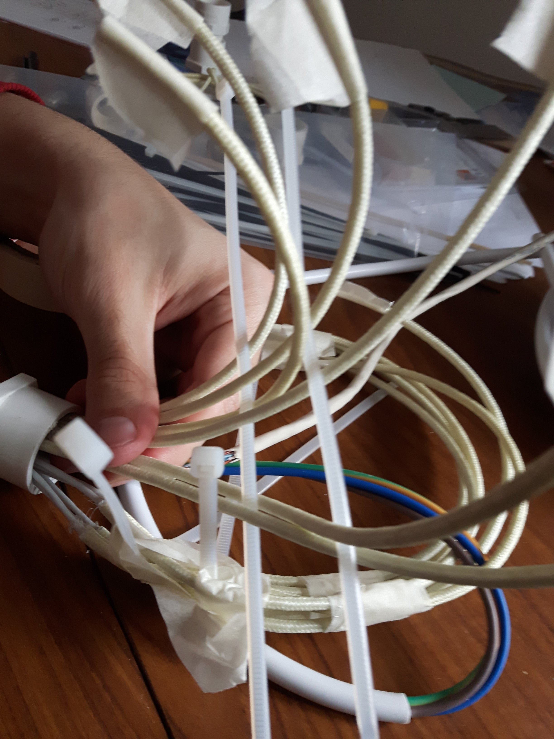
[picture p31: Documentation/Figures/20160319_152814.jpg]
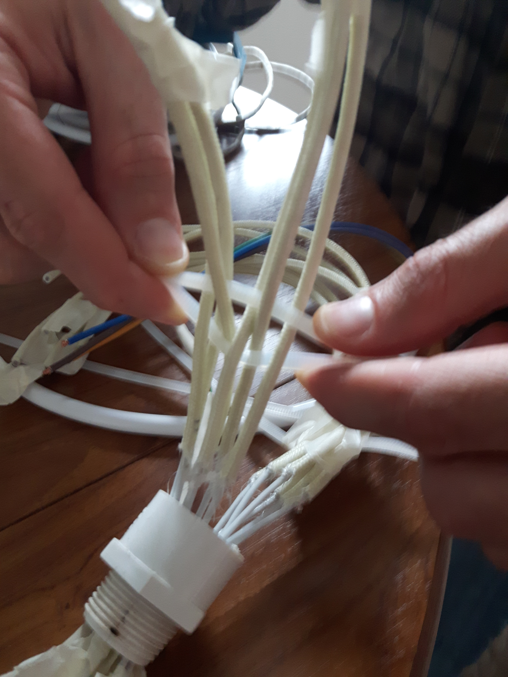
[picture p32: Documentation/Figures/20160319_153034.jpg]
	 &  \\
\end{tabular}
\end{center}
\caption{Before laminating the wires into the PVC connector, they are separated to make sure some resin surrounds every wire and makes a~seal.}
\label{fig:separatingTheWires}
\end{figure}

\clearpage % Place these figures close to the text.

%-------------------------------------------------------------------------------
\subsection{Tether}\label{ssection:tether}
The umbilical tether consists of a~CAT5 cable, which extends the USB bus from the shore-based laptop to the ROV, as well as a~\unit[16]{A}-rated, three-chord power cable, which delivers battery power to the vehicle and grounds its structure. These two cables are held together by a~\unit[6]{mm} diameter nylon rope, which is tied around both cables at intervals of approximately one metre. The nylon rope can also be used to lift the vehicle or recover it from the water in case of failure. To this end, the nylon rope is mounted to the external steel structure of the ROV close to its centre of buoyancy. The steel structure provides a~strong mounting point, and the attachment location minimises the moments that the tether imparts on the vehicle, which makes it easier to operate. The location of the tether and the way it is attached to the ROV is shown in Fig.~\ref{fig:thetherOverview}.

During the initial towing tank test, described in section~\ref{section:manoeuvringTests}, it was discovered that the tether was too heavy and thus caused the ROV to sink, even though it was first made neutrally-buoyant on its own. To remedy this, bubble wrap was tied around the tether to increase its buoyancy. The bubble wrap was fixed with water-proof duct tape, as can be seen in Fig.~\ref{fig:thetherOverview}.

\begin{figure}[htb]
\begin{minipage}[b]{1\linewidth}
  \centering
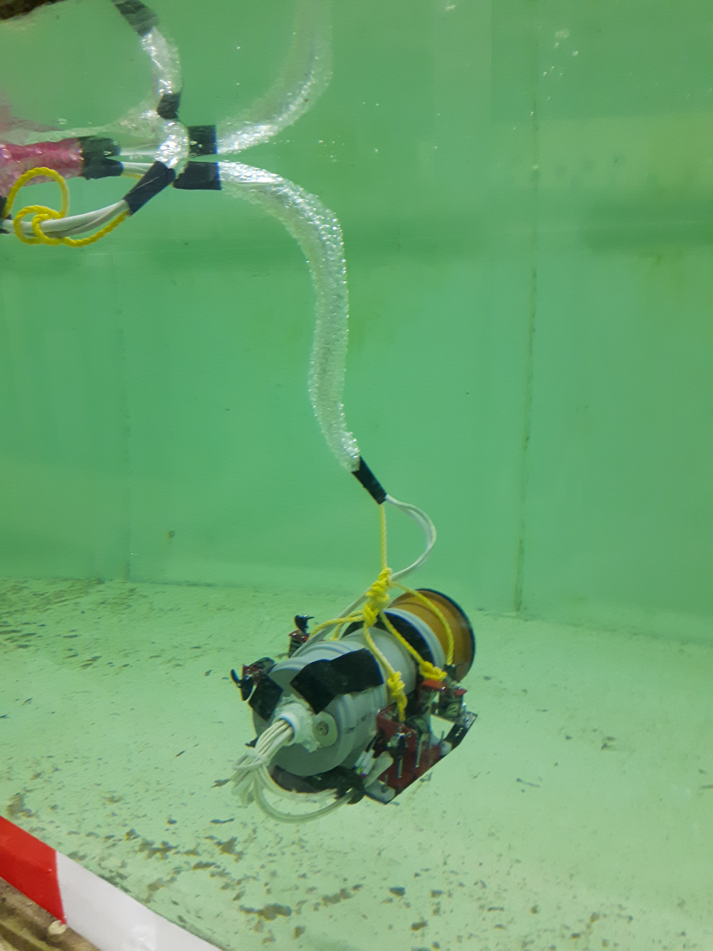
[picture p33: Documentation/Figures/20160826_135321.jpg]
	
\end{minipage}
\caption{Overview of the tether structure together with its attachment to the external steel structure.}
\label{fig:thetherOverview}
\end{figure}

\clearpage % Avoid "too many unprocessed floats" error.

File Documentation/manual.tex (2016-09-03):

\documentclass[11pt,a4paper,oneside]{report}

%%% Title of this document, updated automatically in the title page and references
\title{Design review and recommendations}

\makeatletter
\let\documenttitle\@title
\makeatother

%%% PACKAGES
\usepackage[	bookmarks,%
		breaklinks,%
		backref=false,%
		pdfhighlight=/I,%
		pdffitwindow=true,%
		pdfstartview=Fit,%
		pdfcenterwindow=true,%
		%linkbordercolor={0.4 0.4 1},% change border colour
		colorlinks = false, % switch off colour linked text
		pdfborder={0 0 0}, % switch off colour linked text
		pdftitle=\documenttitle,%
		pdfauthor=Artur K. Lidtke and Aleksander A. Lidtke]%
		{hyperref} % cross-refenreces
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
    numberstyle=\tiny\color{codegray},
    stringstyle=\color{codepurple},
    basicstyle=\footnotesize,
    breakatwhitespace=false,         
    breaklines=true,                 
    captionpos=b,                    
    keepspaces=true,                 
    showspaces=false,                
    showstringspaces=false,
    showtabs=false,                  
    tabsize=2
}
 
\setcounter{tocdepth}{2} % exclude subsubsections from the ToC

\usepackage{hhline} % double line in tables
\usepackage{array} % table formatting
\usepackage{float} % for figures in tabular form
\usepackage{subfig} % --||--
\usepackage{xspace} % smartly add or not a space at the end of macro expressions

\usepackage{fancyhdr} % header/footer
\usepackage{emptypage} % empty cleardoublepage
\usepackage{etoolbox} % change page format using patchcmd

\usepackage{titlesec} % detailed formatting of specific headings
\usepackage{pdfpages}

\usepackage{units}

\graphicspath{{Figures/}} % where all the Figures are held

\allsectionsfont{\sffamily} % set sections font to helvetica
\renewcommand{\bibname}{References}

%%% Macro definitions for Commonly used symbols
\newcommand{\etal}{{\it et al.}\xspace}

%%% Header and footer
\renewcommand{\chaptermark}[1]{\markboth{#1}{}} % keep chapter name with the chapter mark

\fancypagestyle{chapter-fancy-style}{ % used for each page inside the chapters
  \fancyhf{}% Clear header and footer
  \fancyhead[RE,LO]{\large{\documenttitle}} % left odd, right even - chapter title
  \fancyhead[LE,RO]{\large{
   % The chapter number only if it's greater than 0
   \ifnum\value{chapter}>0 \chaptername\ \thechapter. \fi
   % The chapter title
   \leftmark}} % left even, right odd
  \fancyfoot[RE,LO]{}
  \fancyfoot[LE,RO]{\thepage}
  \renewcommand{\headrulewidth}{0.4pt}% Line at the header visible
  \renewcommand{\footrulewidth}{0.4pt}% Line at the footer visible
}

\fancypagestyle{plain}{ % used for 1st page of each chapter
  \fancyhf{}% Clear header and footer
  \fancyhead[RE,LO]{\large{\documenttitle}} % left odd, right even - chapter title
  \fancyfoot[RE,LO]{}
  \fancyfoot[LE,RO]{\thepage}
  \renewcommand{\headrulewidth}{0.4pt}% Line at the header visible
  \renewcommand{\footrulewidth}{0.4pt}% Line at the footer visible
}

%%% PAGE LAYOUT - GENERAL
\setlength{\topmargin}{-0.5cm}
\setlength{\oddsidemargin}{0cm}
\setlength{\evensidemargin}{0cm}
\setlength{\textheight}{24cm}
\setlength{\textwidth}{16cm}

\setlength{\parindent}{0pt} % disable intendation
% paragraph spacing; give a margin on how much it may be changed -> better layout
\setlength{\parskip}{5pt plus 1pt minus 1pt} 

\raggedbottom
\setlength{\topskip}{1\topskip plus 5pt}
\doublehyphendemerits=10000       % No consecutive line hyphens.
\brokenpenalty=10000              % No broken words across columns/pages.
\widowpenalty=9999                % Almost no widows at bottom of page.
\clubpenalty=9999                 % Almost no orphans at top of page.
\interfootnotelinepenalty=9999    % Almost never break footnotes.

% change chapter title format
\titleformat{\chapter}[hang] {\sffamily\huge\bfseries}{\chaptertitlename\ \thechapter:}{20pt}{}
% change whitespace before and after \chapter, \section etc.
\titlespacing*{\chapter}{0pt}{-15pt}{10pt} % left, upper, lower
\titlespacing{\section}{0pt}{5pt}{5pt}
\titlespacing{\subsection}{0pt}{2pt}{2pt}
\titlespacing{\subsubsection}{0pt}{2pt}{2pt}

%%% Table formatting
\newcolumntype{Y}{>{\centering\arraybackslash}X} % expended column to fit page, centred horizontally
\newcolumntype{C}{>{\centering\arraybackslash}m{3cm}} % wrapped text, fixed width column, centred vertically
\newcolumntype{+}{>{\global\let\currentrowstyle\relax}}% start a custom formatted row
\newcolumntype{^}{>{\currentrowstyle}} % column in a custom row
\newcommand{\rowstyle}[1]{\gdef\currentrowstyle{#1}#1\ignorespaces} % applies format to the entire row

%\usepackage{draftwatermark}
%\SetWatermarkText{DRAFT}
%\SetWatermarkScale{1}
%\SetWatermarkLightness{0.9}

\begin{document}

%%% Title, contents, abstract, etc.
\include{titlePage/titlePage}

\include{chapters/abstract}

\pagenumbering{Roman}

% create table of contents and add it to bookmarks for easier navigation in the PDF
\tableofcontents
\addtocontents{toc}{\protect{\pdfbookmark[0]{\contentsname}{toc}}}
\listoffigures
\listoftables

%%% Prepare formatting for main body
\patchcmd{\chapter}{plain}{fancy}{}{} % 1st page of each chapter is set to plain by default, change this
\pagestyle{fancy} % change page style from default "plain" to accommodate new header/footer settings

\setcounter{page}{1}
\pagenumbering{arabic}

\onehalfspacing

%%% Main body of the report
\include{chapters/introduction}

\include{chapters/manufacturingAndAssembly}
\include{chapters/softwareDesign}
\include{chapters/testing}

%%% Conclusions
\include{chapters/conclusions}

%\bibliography{../library}{}
%\bibliographystyle{ieeetr}

%%% Appendix
\begin{appendix}

\end{appendix}

\end{document}

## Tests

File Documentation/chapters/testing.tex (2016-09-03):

\pagestyle{chapter-fancy-style}
\chapter{Testing}

%=====================
\section{Procedure}

The first stage of in-water tests was carried out in the Lamont
towing tank of the University of Southampton. Figure \ref{fig:testingSetup}
shows the experimental set-up used in the described tests.
The towing tank provided a~calm, controlled
environment without currents or wind. The water depth was under \unit[2]{metres},
which was deemed sufficient for the initial test of the pressure vessel.
Furthermore, the window in the side of the towing tank allowed easier observation
of the robot from the side.

There were three main tests to be carried out during the first series of testing:
\begin{enumerate}
\item  Testing of the power output of all the motors and making sure they can drive
	the vehicle in a steady and controlled manner. If not, adjusting the control
	inputs to compensate for any asymmetries
\item Verifying that the provided visual cues, proposed control interface, and
	available motor arrangements are suitable to allow a new user to operate the
	vehicle efficiently and perform simple tasks, such as inspection of underwater
	objects
\item Submerging the vehicle to progressively larger depths to test the water-
	tightness of the outer hull
\end{enumerate}

\begin{figure}[htb]
\begin{center}
\begin{tabular}{c c}
	\subfloat[Dry and manoeuvring tests]
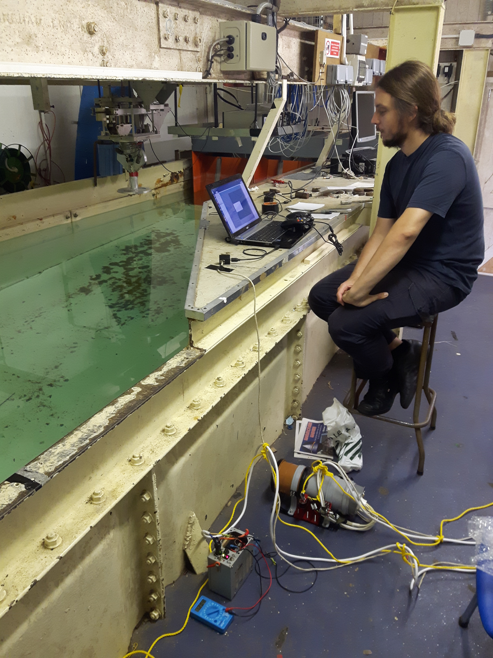
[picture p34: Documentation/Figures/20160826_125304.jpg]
		{
		\label{figure:testingSetup:label:a} } &
	\subfloat[For observation through side window]
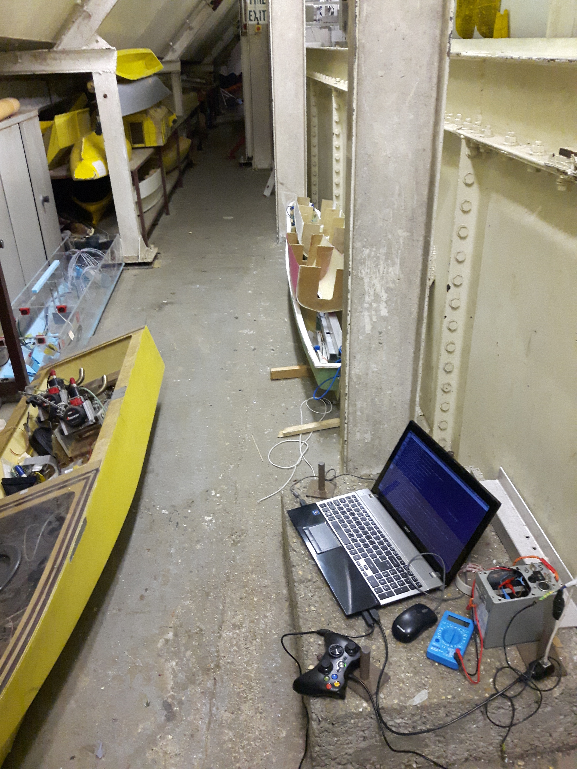
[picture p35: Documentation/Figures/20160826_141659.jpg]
		{
		\label{figure:testingSetup:label:b} } \\
\end{tabular}
\end{center}
\caption{View of the testing set-up in the Lamont towing tank.}
\label{fig:testingSetup}
\end{figure}

In order to comply with the health \& safety regulations, a strictly defined
procedure of using the ROV was put in placed and adhered to throughout the testing:
%
\begin{enumerate}
\item Plugging the ROV into a laptop via an Ethernet cable using a USB converter
\item Powering-up the motors using a 12 V DC power supply placed on-shore
\item Testing the camera system and ensuring each of the motors is operational
\item Placing the vehicle in the water using an insulated rod and an attachment point
	provided by the main tether
\item Performing the required tests and tasks
\item Surfacing the vehicle close to the operator and unplugging the power supply
\item Recovering the vehicle by hand and finishing the test
\end{enumerate}

%=====================
\section{Manoeuvring tests}\label{section:manoeuvringTests}

Before the towing tank tests it had been recognised that despite all electric
motors and electronic speed controllers being identical, the same demand signals
from the Arduino board made each of the motors rotate at a slightly different
speed. This had been identified by setting them to the highest RPM in pairs
and listening to the sound they produce while adjusting the tuning constants in order to eliminate the beat frequency (much like tuning a guitar). One of the
vertical thrusters proved to behave particularly differently than the others.
Its tuning parameters were thus adjusted in the Arduino script before the tests,
in order to achieve approximately identical RPM as the other vertical motor
with the same thrust demand.

Once the vehicle was placed in water its balance, initially tested in a small
water container, was verified. The predicted centre of gravity location agreed
well with the expectations, yielding neutral trim. At the outset of the tests
the vehicle was also neutrally buoyant and kept a steady altitude just below the
water surface. Placing the tether attachment at the centre of gravity negated
any moments and prevented the ROV from adopting excess trim angles.
At first, however, the tether was not as buoyant as initially hoped and was dragging
the robot down to the bottom. An impromptu solution was employed whereby sheets
of bubble wrap were attached at even intervals to the tether, making it neutrally
buoyant.

Then, several basic manoeuvres were attempted:
moving in a straight line horizontally and in the vertical plane, orienting the
ROV in a particular direction, and turning while under way.
It has been found that the used motors and propellers provide more than enough
thrust to make the vehicle agile and faster than expected. The control interface
also fulfilled its purpose well and allowed the operator to convey commands to
the ROV with ease. An example of a successful descent manoeuvre is seen in
Figure \ref{fig:rovThroughTheWindow}.
Due to the linear mapping of the joystick displacement to
thrust demand it was rather difficult for the operator to execute very precise
control over the vehicle, however. Such precise control requires very low levels
of thrust, which can only be obtained with minimal joystick displacements in the
current implementation.

It was also found that the tether, in particular the power cable, was so
stiff and twisted (it had spent most of its lifetime on a~reel prior to deployment)
that it made it difficult for the ROV to move freely. This is because the
twist in the tether exerted a~constant moment on the robot, which in turn
rotated the ROV around the tether. This meant that adopting
certain headings was impossible without constant actuation of the thrusters, for example.

It had also been expected that the load on the motors would increase significantly
when they operated in water instead of air, which was indeed observed. At first,
the battery system had been fitted with \unit[1]{A} fuse, which was sufficient
to operate four motors at their maximum thrusts in air. In water, however, 
the \unit[1]{A} fuse allowed the user to only operate the motors at very low RPMs
and made it difficult not to exceed the current limit, thus requiring a~fuse
replacement. In practice, only a~small deviation in the joystick position would
lead to burning the fuse. The internal electronics were capable of
sustaining higher currents and the \unit[1]{A} limit had been chosen somewhat
arbitrarily for increased safety. The safety concern was relaxed during the test
and a~\unit[4]{A} fitted instead. This allowed the user to operate the ROV 
without any restraint while still having a~safeguard built into the system.

\begin{figure}[htb]
\begin{center}
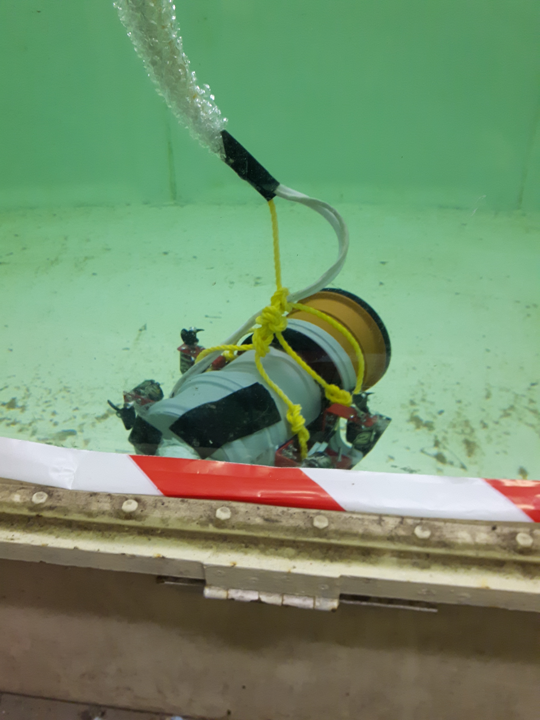
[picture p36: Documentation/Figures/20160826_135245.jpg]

\end{center}
\caption{ROV floating near the bottom of the towing tank.}
\label{fig:rovThroughTheWindow}
\end{figure}

%=====================
\section{Blind control tests}

Outside of control environment, the operator would not be able to see the ROV from their
workstation and instead they would have to rely solely on the visual and other
cues fed back to them from the on-board sensors. The next stage of tests focused
on simulating this scenario by placing the operator so that the ROV was outside
their field of view. They were then tasked with performing the same tasks as before
(simple manoeuvres - straight line, turning circle, ascent/descent, keeping
a constant heading) when relying only on the video feed from the USB camera
fitted to the ROV.

It has been found that latency present in the visual system was detrimental to
the user's ability to manoeuvre the vehicle easily. They were able to establish
the general direction the ROV was facing in relation to the main features of the
nearby environment. Doing so required them to put in considerable effort and
was further made difficult by the unpredictable forces and moments exerted by
the tether. The exact reason for the existence of latency in the video feed is
unclear - it could be due to the camera itself, due to the same CAT5 cable being
used to transfer video and serial commands to the Arduino, due to some issues
with the OpenCV library and its implementation in the current code, or due to
limitations of the current graphical user interface design.

Furthermore, it has been found that the 640x480 resolution of the camera is not
sufficient to provide detailed view of the ROV surroundings when the vehicle is
put in water with particulates in it. This made it difficult to judge the distance
of the vehicle from the obstacles ahead by using visual cues only.
Nonetheless, enough detail could be captured to allow key environmental
features to be distinguished, as seen in Fig.~\ref{fig:onBoardPictures}.

Lastly, the camera has a~considerable zoom. This makes approaching a~target at 
a~close distance dfficult because it seems to be much larger and thus closer than it in fact is.
At present, none of the ROV components are visible in the camera field of view.
Changing this, for example by using a~camera with a~wider field of view and moving
it further away from the pressure vessel surface, could help the operator judge
proximity to obstacles. This is because both the visible ROV components and the
obstacles would be distorted by the camera in the same way, and the relative
distance could be assessed.

\begin{figure}[htb]
\begin{center}
\begin{tabular}{c c}
	\subfloat[ROV on the free surface]
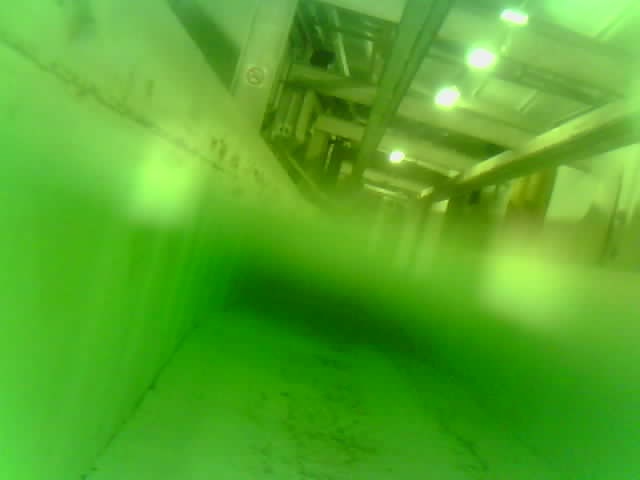
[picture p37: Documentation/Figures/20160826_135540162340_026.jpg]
		{} &
	\subfloat[Wavemakers at the end of the tank]
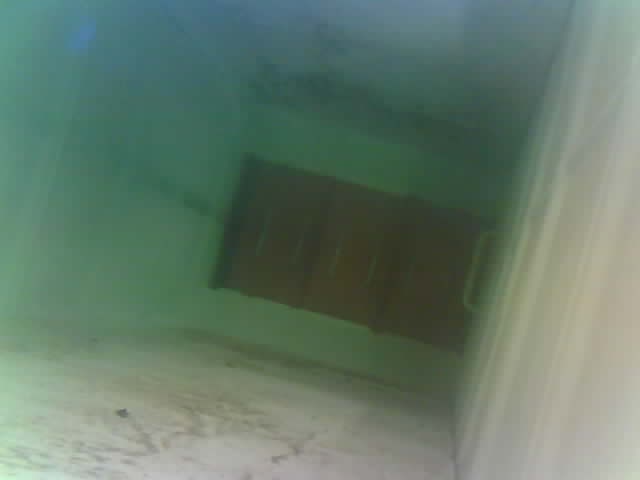
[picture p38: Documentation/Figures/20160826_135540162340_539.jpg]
		{} \\
	\subfloat[Operators seen through the side window of the tank]
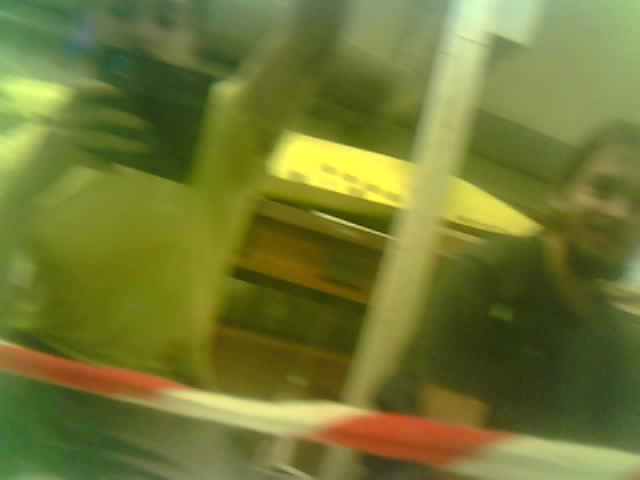
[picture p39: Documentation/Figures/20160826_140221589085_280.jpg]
		{} &
	\subfloat[The far end of the tank]
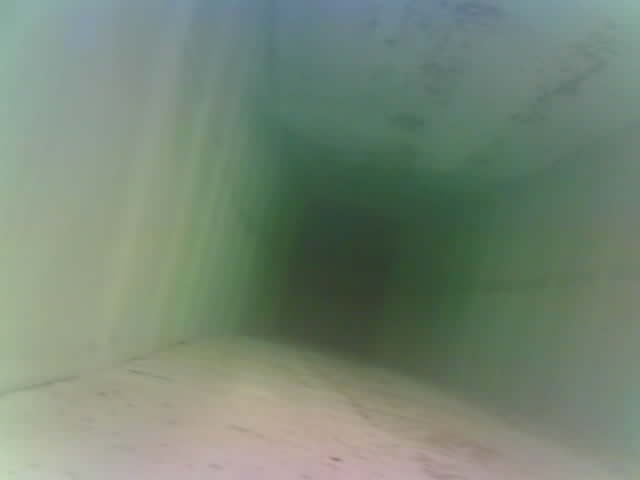
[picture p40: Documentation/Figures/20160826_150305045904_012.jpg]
		{} \\
\end{tabular}
\end{center}
\caption{Video frames captured by the on-board camera during towing tank tests.}
\label{fig:onBoardPictures}
\end{figure}

%=====================
\section{Water-tightness tests}

Before the tests in the towing tank, the ROV had been submerged in a small water
container (i.e. a bath tub) for the period of several hours to verify the efficacy
of seals and connections. No water ingress had been observed even for overnight
immersion tests at the depth of approximately 30 cm.

The towing tank tests lasted approximately 3.5-4 hours, during which the ROV
was removed from the water several times. After the initial several seconds
after the first immersion no visible water bubbles were seen escaping from the
hull, indicating the hull remained watertight.
Throughout the tests, however, the vehicle was observed to gradually lose its
neutral buoyancy. Towards the end of the trials, the ROV would linger close to the
tank bottom, and making it ascend using the thrusters alone became difficult.
After the final test run, the aft plug was removed and a~small amount of water was
seen to leak from inside the pressure vessel. The exact volume was not verified due to lack of
experience of the operators. It was sufficient to adversely affect the neutral buoyancy
of the vehicle but did not reach the electronics, which suggests the leak was
small. It is believed the water ingress took place through the aft seal between
the hull and removable aft plug as it was at this location that small air bubbles
were seen escaping at the beginning of each series of tests.
The aft cable port could also be the culprit, although this is seen as less likely.

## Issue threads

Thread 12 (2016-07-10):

Add a buffer for images

AleksanderLidtke, 2016-07-10:
Add a buffer where images from the camera will be temporarily stored. Only saye them to hard drive every so often not to block the main thread.

UnnamedMoose, 2016-07-13:
Sorted it out.

Closed 2016-07-13.

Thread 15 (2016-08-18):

Fix the sizers

AleksanderLidtke, 2016-08-18:
For some reason, the sizers in the rovGuiMainFrame don't work too great for me:
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

AleksanderLidtke, 2016-09-03:
Fixed this by wrapping long controller names to a fixed width (predefined no. characters). This could be made prettier, though.
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

Closed 2016-09-03.

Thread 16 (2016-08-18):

Change ballast screws for leftover steel and aluminium

AleksanderLidtke, 2016-08-18:
At present, the ballast on the bow is jury-rigged (ekhem, bodged together). Make it neater.

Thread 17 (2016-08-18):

Change the aft banana connectors for one plug

AleksanderLidtke, 2016-08-18:
Connecting all the engine harness with banana connectors is a pain and creates room for error - deal with this by adding a plug and a socket that'd mate the mosfet PCB outputs with the right inputs into the engines. Something like [this](http://uk.rs-online.com/web/p/automotive-connectors/7242579/) should work.

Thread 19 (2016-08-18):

Make the engines watertight

AleksanderLidtke, 2016-08-18:
This is a tricky one, and probably requires some research into magnetic coupling and manufacture of dedicated, water-tight engine housings.

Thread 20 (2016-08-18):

Make the aft plug screw-on

AleksanderLidtke, 2016-08-18:
Currently, the assembly is complicated, and water-tightness of the aft plug can be compromised by the plug not being mounted correctly (or the duct tape giving up :P ). This could all be fixed by changing the plug to a screw-on version, something like the plug in [this](http://www.wickes.co.uk/Wickes-110mm-Grey-Soil-Access-Pipe/p/158919). This might require an interior overhaul, however, if we cannot get a plug that screws into the end of the pipe instead of in the side.

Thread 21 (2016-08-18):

Put ESCs on a PCB

AleksanderLidtke, 2016-08-18:
Put ESCs on a dedicated PCB to remove harness between them and the relays. This will reduce the mass of the ROV and make the assembly easier. Could use this [IC from TI](http://www.ti.com/product/DRV10983/datasheet/abstract#SLVSCP22742), or something similar (more research on components and prototyping are required). Possibly, use stackthrough connectors (e.g. [Samtec's ESQ](https://www.samtec.com/products/esq?gclid=CKuU_M6Ay84CFawp0wodc14Jkg)) to build a stack of boards like this:
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

AleksanderLidtke, 2016-08-18:
Could even go flat-out and build a stack of boards for the entire ROV, connected to the Arduino as a shield. This would eliminate most of the harness, and make the craft smaller and easier to assemble.

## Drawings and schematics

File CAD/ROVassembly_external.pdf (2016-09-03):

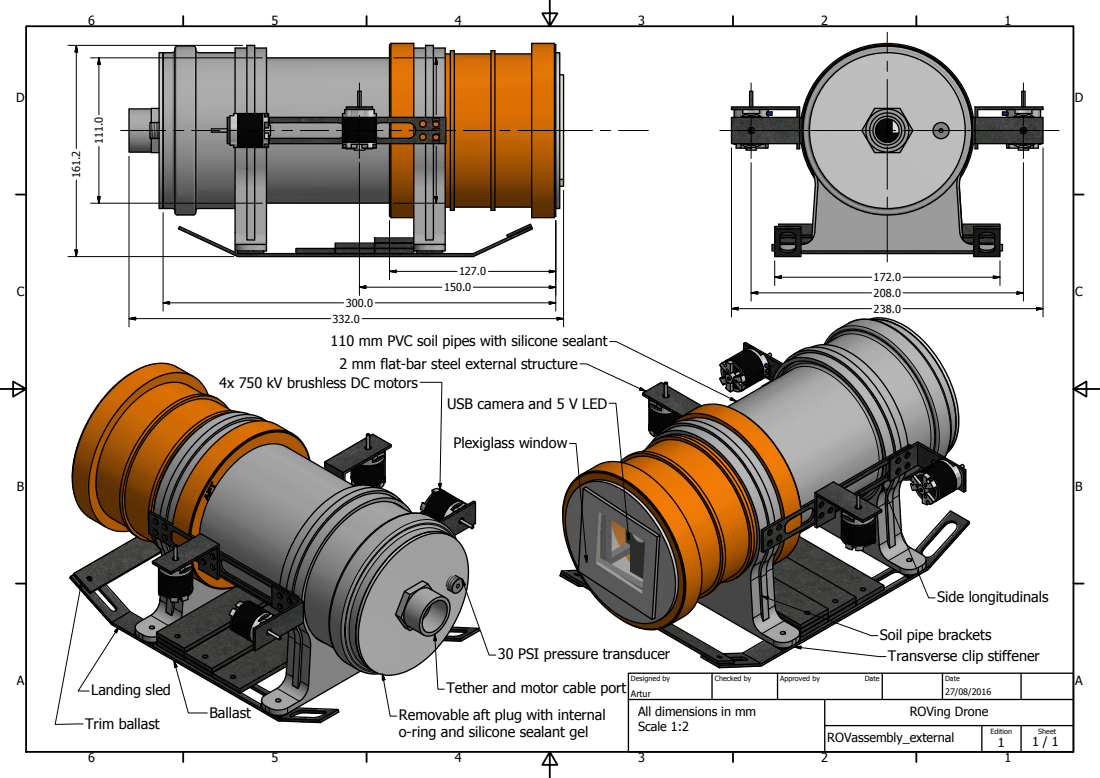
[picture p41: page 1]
ROVing Drone; ROVassembly_external; Artur; Designed by; Checked by; Approved by; Date; Edition; Sheet; Ballast; Landing sled; Plexiglass window; Trim ballast; Side longitudinals

110 mm PVC soil pipes with silicone sealant
2 mm flat-bar steel external structure

4x 750 kV brushless DC motors

USB camera and 5 V LED

Soil pipe brackets
Transverse clip stiffener

30 PSI pressure transducer

All dimensions in mm
Scale 1:2

Tether and motor cable port

Removable aft plug with internal
o-ring and silicone sealant gel

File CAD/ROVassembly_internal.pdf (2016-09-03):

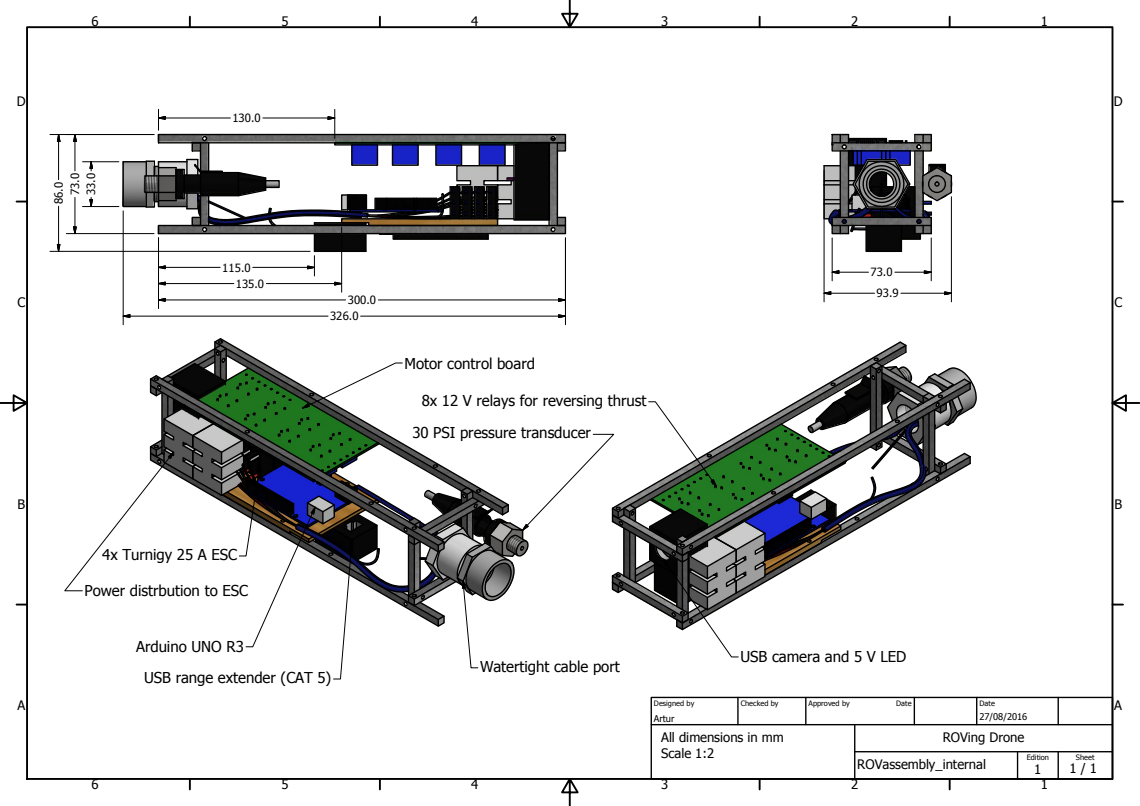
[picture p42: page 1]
ROVing Drone; ROVassembly_internal; Artur; Designed by; Checked by; Approved by; Date; Edition; Sheet; Arduino UNO R3; 4x Turnigy 25 A ESC

Motor control board

8x 12 V relays for reversing thrust

30 PSI pressure transducer

Power distrbution to ESC

USB camera and 5 V LED

Watertight cable port

USB range extender (CAT 5)

All dimensions in mm
Scale 1:2

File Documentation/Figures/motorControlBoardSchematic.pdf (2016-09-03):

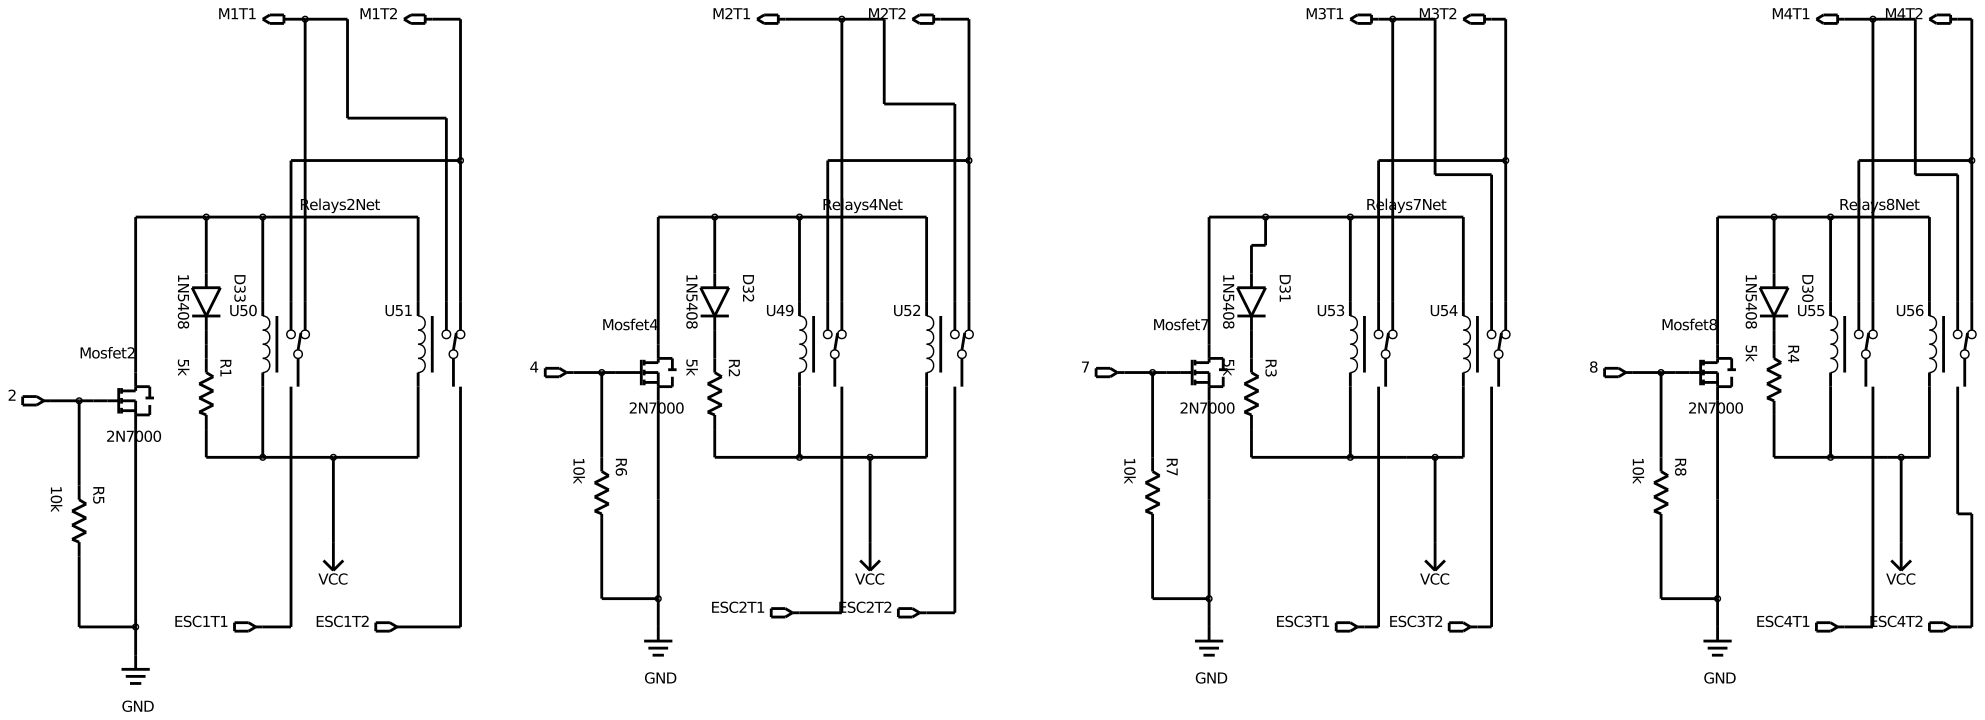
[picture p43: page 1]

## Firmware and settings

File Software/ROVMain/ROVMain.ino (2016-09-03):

/* A main application running on the Arduino that accepts telecommands from the
 * PC sent over serial, interprets them, conducts the required actions and sends
 * the required data back.
 * 
 * The telecommands follow a specified, custom protocol with a special character
 * at the beginning and end of every command. Every command can have a number of
 * strings that identify actions, followed by values (arguments for the actions).
 *
 * @author: Aleksander Lidtke
 * @email: alekasdner.lidtke@gmail.com
 * @url: www.aleksanderlidtke.com
 * @since: 10 Jul 2016
 * @version: 2.2.0
 */

//#define DEBUG_PRINTOUT // this will cause issues with arming modules as the GUI expects a delay in ms to be returned upon sending "armModules,1"; either fix or don't use the GUI in conjuction with this flag

// Custom includes.
#include "Module.h"
#include "BrushlessDCMotor.h"
#include "DepthSensor.h"
#include "Servo.h"
#include "LEDModule.h"

// Standard C/C++ includes
#include <stdio.h>

// ROV identifiers.
const String ROV_MODEL = "ROVing Drone";
const String ROV_SW_VERSION = "2.2.0r";

/* =============================================================================
 * FUNCTION DECLARATIONS.
 * =============================================================================
 */
void parseInput(void);
boolean getSerial(void);
void sendSensorReadings(void);
void armModules(void);
void armActuator(int idx);

/* =============================================================================
 * MOTOR DEFINITIONS.
 * =============================================================================
 */
// These values correspond to the currently selected electronic speed controller (ESC) - Turningy EA-25a.
#define MOTOR_ARM_PULSE_WIDTH 1100 // Pulse width in microseconds corresponding to zero throttle; used to arm the motors.
#define MOTOR_MAX_PULSE_WIDTH 2200 // Maximum pulse width of the motor in microseconds.
#define MOTOR_MIN_PULSE_WIDTH 800 // Minimum pulse width of the motor.
#define THROTTLE_STEPS 100 // How many levels of throttle we want to have.

// Pins are pairs of close-by pins with PWM and digital ones.
BrushlessDCMotor engine1 = BrushlessDCMotor("motorPortHor", THROTTLE_STEPS, MOTOR_MAX_PULSE_WIDTH,
	MOTOR_MIN_PULSE_WIDTH, MOTOR_ARM_PULSE_WIDTH, 3, 2); // orange // 1st-pwm, 2nd-digital
BrushlessDCMotor engine2 = BrushlessDCMotor("motorStbdHor", THROTTLE_STEPS, MOTOR_MAX_PULSE_WIDTH,
	MOTOR_MIN_PULSE_WIDTH, MOTOR_ARM_PULSE_WIDTH, 5, 4); // green
BrushlessDCMotor engine3 = BrushlessDCMotor("motorPortVer", THROTTLE_STEPS,MOTOR_MAX_PULSE_WIDTH,
	MOTOR_MIN_PULSE_WIDTH, MOTOR_ARM_PULSE_WIDTH, 6, 7); // white
BrushlessDCMotor engine4 = BrushlessDCMotor("motorStbdVer", THROTTLE_STEPS,
	2050, 950, 1200, 9, 8); // blue

/* =============================================================================
 * MISC ACTUATOR AND COMMAND DEFINITIONS.
 * =============================================================================
 */
Module armModulesModule = Module("armModules"); // Arms all the sensors and actuators.
Module armActuatorModule = Module("armActuator"); // Arms only one of the actuators depending on the argument it receives.

Module sendSensorReadingsModule = Module("sendSensorReadings"); // Sends sensor readings over serial.

Module refreshRate = Module("refreshRate"); // Changes the delay in the main loop.

LEDModule forwardLED = LEDModule("forwardLED", 12); // Switches the forward illumination LED, on pin 12, on or of.

const int ON_LED_PIN = 13; // LED on the Arduino board that will be lit when the ROV is in the main loop.

/* =============================================================================
 * SENSOR DEFINITIONS.
 * =============================================================================
 */
// TODO depth sensor plugged in to analog A0 pin
DepthSensor depthSensor = DepthSensor("depthReading",15); // For now a mock sensor.
DepthSensor depthSensor2 = DepthSensor("depthReading2",16); // Another mock sensor to make sure the message concatenation works well.

/* =============================================================================
 * TELECOMMAND PROTOCOL DEFINITION.
 * =============================================================================
 */
// Input and output data buffers.
#define DATABUFFERSIZE 180
char inputDataBuffer[DATABUFFERSIZE+1]; // Where the received command will be temporarily held. Add 1 for NULL terminator at the end.
String outputDataBuffer = ""; // We'll store a message here before sending it.

// Data chunk delimiters - used to split commands and values that follow them.
const char INPUT_START_CHAR = '>'; // At the start of every command message sent TO the Arduino.
const char OUTPUT_START_CHAR = '<'; // At the start of every command message sent FROM the Arduino.
const char END_CHAR = ';'; // End of the command message sent to and from the Arduino.
const char DATA_DELIMITER[2] = ","; // Splits the command name and value. For some reason has to be size 2.

Module* actuators[] = {&armModulesModule, &armActuatorModule, &engine1, &engine2, &engine3, &engine4, &sendSensorReadingsModule, &refreshRate, &forwardLED};
Module* sensors[] = {&depthSensor, &depthSensor2};

/* =============================================================================
 * MAIN FUNCTIONS DEFINITIONS.
 * =============================================================================
 */
void setup(void)
/* Prepare to listen to commands over serial and start everything up. */
{
	armModulesModule.setValue(0); // Don't arm the modules by default, wait for a command.
	armActuatorModule.setValue(-1); // Will arm the actuator that's under the index of armActuatorModule value.
	refreshRate.setValue(10); // Set default delay in milliseconds in the main loop
	forwardLED.setValue(0); // LEDs are off by default.
	
	// set modes for pins used by simple switch modules
	pinMode(ON_LED_PIN, OUTPUT);

	//TODO: do some system checks, like battery level, connections etc.

	// Start serial comms at the same baud rate as the engines.
	Serial.begin(engine1.serialBaudRate);
	
	Serial.println("ROV "+ROV_MODEL+" v. "+ROV_SW_VERSION+" listening to commands.");
}

void loop(void)
{
	// Light the LED to show the ROV is working and executing the main loop.
	digitalWrite(ON_LED_PIN, HIGH);

	// Get and set control inputs.
	if ( Serial.available())
	{
		if (getSerial()) // If we got a command over serial read it into the inputDataBuffer char array.
		{
			parseInput(); // Parse the telecommand and set appropriate actuator values.
		}
	}

	// Arm the modules if requested.
	if(armModulesModule.getValue()==1)
	{
		armModules(); // This function handles everything.
		armModulesModule.setValue(0); // We're done arming now.
	}
	
	// Arm the engine that was requested.
	if(armActuatorModule.getValue()!=-1)
	{
		// Arm whatever module the user wants.
		armActuator(armActuatorModule.getValue());
		armActuatorModule.setValue(-1); // Go back to default value.
	}
	
	// Send readings from all the sensors over serial after this has been requested by a command.
	if(sendSensorReadingsModule.getValue()==1)
	{
		sendSensorReadings(); // Send the readings.
		sendSensorReadingsModule.setValue(0); // Re-set the flag and wait for it to be send next time readings are required.
	}
	
	// Reduce rate at which stuff happens.
	delay(refreshRate.getValue());
}

/* =============================================================================
 * HELPER FUNCTIONS DEFINITIONS.
 * =============================================================================
 */

boolean getSerial(void)
/* Read input from the serial port and store it in the inputDataBuffer buffer.
 * The serial input has to conform to a protocol, whereby the messages begin with
 * INPUT_START_CHAR and terminate with END_CHAR. The message in between is
 * a sequence of strings and integers. Strings represent the destination of the 
 * command (e.g. engine throttle) and integers are the arguments for the command
 * (e.g. throttle value).
 *
 * @return - true if we've parsed the entire command successfully; false otherwise,
 * 			e.g. when we didn't receive a command.
 */
{
	static boolean placeInBuffer = false; // Only write data when working on a recognisable data chunk
	static byte dataBufferIndex = 0;
	char incomingbyte; // The currently read serial input byte.
	
	while(Serial.available()>0)
	{
		incomingbyte = Serial.read(); // Read bytes from the serial input one by one.

		if(incomingbyte==INPUT_START_CHAR) // A command has been received.
		{
			dataBufferIndex = 0; // We'll be reading the first input value next.
			placeInBuffer = true; // We should be storing the inputs in the buffer now.
		}

		if(placeInBuffer)
		{
			if(dataBufferIndex==DATABUFFERSIZE)
			{
				// Index is pointing to an array element outside our buffer.
				dataBufferIndex = 0; // We're done reading this command, so have to start reading the next one from the beginning.
				break; // Exit the while loop, we're done with this command.
			}
		
			if(incomingbyte==END_CHAR) // We've reached the end of this command.
			{
				inputDataBuffer[dataBufferIndex] = 0; // Null terminate the C string
				placeInBuffer = false; // Don't store anything here any more.
				dataBufferIndex = 0; // Make sure next command gets written to the start of the buffer.
				return true; // Say that we've parsed the whole command.
			}
			else if (incomingbyte!=INPUT_START_CHAR) // Simply record the telecommand byte.
			{
				inputDataBuffer[dataBufferIndex++] = incomingbyte;
			}
		}
	}

	return false; // Something went wrong or we didn't receive an actual command.
}

void parseInput(void)
/* Extract commands and corresponding numbers from the inputDataBuffer input buffer. */
{
  // Get the first data token.
  char * token;
  token = strtok(inputDataBuffer, DATA_DELIMITER);
  
  // Parse the entire inputDataBuffer of tokens (commands and their value arguments).
  int nextActuatorIndex = -1; // Index of the actuator value for which is sent in this part of the telecommand.
  
  while (token != NULL)
  {
  	// If next actuator index < 0 we have no value to read now
  	if (nextActuatorIndex >= 0)
  	{
  		#ifdef DEBUG_PRINTOUT
	  		Serial.print("ROV "+ROV_MODEL+" v. "+ROV_SW_VERSION+" trying to set value of actuator ");
	  		Serial.print(actuators[nextActuatorIndex]->getIdentifier());
	  		Serial.print(" to ");
	  		Serial.println( String(int(atof(token))) );
  		#endif
  		
  		actuators[nextActuatorIndex] -> setValue( int(atof(token)) );
  		// Indicate that on the next pass there is no value to read.
  		nextActuatorIndex = -1;
	}
	else
	{	
	  // Check what value is coming next strings
	  for(long int actuatorI=0;actuatorI<sizeof(actuators)/sizeof(actuators[0]);actuatorI++)
	  {
	  	if (strcmp(token, actuators[actuatorI]->getIdentifier()) == 0)
	  	{
	  		nextActuatorIndex = actuatorI;
	  		break;
	  	}
	  }
	}
        
	// Continue to the new token.
	token = strtok(NULL, DATA_DELIMITER);
  }
}

void sendSensorReadings(void)
/* Send a message over the USB bus according to the agreed telecommunications
 * protocol, containing a series of identifier strings followed by values of the
 * current sensors.
 */
{
	outputDataBuffer += OUTPUT_START_CHAR; // Start the message.
	for(long int i=0;i<sizeof(sensors)/sizeof(sensors[0]);i++)
	{
		outputDataBuffer += String( sensors[i]->getIdentifier() );
		outputDataBuffer += DATA_DELIMITER;
		outputDataBuffer += String( sensors[i]->getValue() );
		if(i<sizeof(sensors)/sizeof(sensors[0])-1) // Don't add a delimiter after the last sensor.
		{
			outputDataBuffer += DATA_DELIMITER;
		}
	}
	outputDataBuffer += END_CHAR; // Terminate the message.
	
	Serial.println( outputDataBuffer ); // Send the formatted message.
	outputDataBuffer = ""; // Restart the buffer so it's clean before sending the next message.
}

void armActuator(int idx)
/* Arm the actuator that's under the input index in the actuators array.
 * int idx - index of the actuators corresponding to the engine that will be armed.
 */
{
	int setupDelay = actuators[idx]->arm(); // Arm only this actuator.
		
	// Send the message saying how long the delay will last.
	outputDataBuffer += OUTPUT_START_CHAR; // Start the message.
	outputDataBuffer += "setupDelay";
	outputDataBuffer += DATA_DELIMITER;
	outputDataBuffer += String(setupDelay);
	outputDataBuffer += END_CHAR; // Terminate the message.
	Serial.println( outputDataBuffer ); // Send the formatted message.
	outputDataBuffer = ""; // Restart the buffer so it's clean before sending the next message.
	
	delay(setupDelay); // Wait for as long as required by the slowest arming module.
}

void armModules(void)
/* Arm all the modules registered in actuators and sensors arrays by calling their
 * arm methods and waiting for the requested duration. Wait for the longest
 * duration necessary to arm any module and send a message over serial saying for
 * how long Arduino  will be sleeping so that the GUI knows.
 */
{
	int setupDelay(0); // By default wait for 0 seconds, i.e. arm nothing.
	for(long int i=0;i<sizeof(actuators)/sizeof(actuators[0]);i++) // Arm all actuators.
	{
		int delayRequested = actuators[i]->arm();
		if (delayRequested > setupDelay) setupDelay = delayRequested;
	}
	for(long int i=0;i<sizeof(sensors)/sizeof(sensors[0]);i++) // Arm all sensors.
	{
		int delayRequested = sensors[i]->arm();
		if (delayRequested > setupDelay) setupDelay = delayRequested;
	}
	
	// Send the message saying how long the delay will last.
	outputDataBuffer += OUTPUT_START_CHAR; // Start the message.
	outputDataBuffer += "setupDelay";
	outputDataBuffer += DATA_DELIMITER;
	outputDataBuffer += String(setupDelay);
	outputDataBuffer += END_CHAR; // Terminate the message.
	Serial.println( outputDataBuffer ); // Send the formatted message.
	outputDataBuffer = ""; // Restart the buffer so it's clean before sending the next message.
	
	delay(setupDelay); // Wait for as long as required by the slowest arming module.
}

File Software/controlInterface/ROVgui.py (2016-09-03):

#!/usr/bin/python
# -*- coding: utf-8 -*-
"""
Created on Sun May 24 16:34:31 2015

@author: Artur, Alek
"""

import ROVguiBaseClasses
import throttleDial
import communicationProtocol
import controllerInterface

import wx, string
from wx.lib import statbmp
import cv2
import os
import serial
import numpy as np
import datetime, multiprocessing
from scipy import interpolate

CONTROLLER_NAME_CHUNK_LENGTH=20 # Have to split controller names into lines, each with at most this many characters.

def savePhotos(imgList,directory):
    """ Save every photo from a list into separate files, the image name will
    contain the current time to make sure nothing is overwritten. Intended to
    be used in a separate process not to block the GUI.
    
    Arguments
    ----------
    imgList - list of images as output of cv2.VideoCapture.read.
    directory - str with the directory where the photo will be written.
    
    Example
    ----------
    p = multiprocessing.Process(target=savePhotos, args=(self.imgBuff,self.videoDirectory))
    p.start() # Don't p.join - will block the GUI thread.
    """
    outName=datetime.datetime.now().strftime("%Y%m%d_%H%M%S%f") # Time stamp the images.
    for i in range(len(imgList)):
        cv2.imwrite(os.path.join(directory,outName)+"_{}.jpg".format(i), imgList[i])

class IntValidator(wx.PyValidator):
    """ Validates data as it is entered into the text controls. """
    def __init__(self):
        wx.PyValidator.__init__(self)
        self.Bind(wx.EVT_CHAR, self.OnChar)

    def Clone(self):
        """ Required Validator method """
        return IntValidator()

    def Validate(self, win):
        return True

    def TransferToWindow(self):
        return True

    def TransferFromWindow(self):
        return True

    def OnChar(self, event):
        """ Do the validation """
        keycode = int(event.GetKeyCode())
        if keycode < 256:
            key = chr(keycode)
            if not key in string.digits: # skip this char since it's not a digit
                return
        event.Skip()

class rovGuiArmDialog( ROVguiBaseClasses.armDialog ):
    """ Halts the application while the arm method is active """
    def __init__(self,delay):
        ROVguiBaseClasses.armDialog.__init__(self,None)
        self.armTimer.Start(delay*1000.0)
    
    def onClose(self,event):
        self.Destroy()

class rovGuiCommunicationsSettingsDialog( ROVguiBaseClasses.communicationsSettingsDialog ):
    """ Allows the user to adjust frequencies of sending and receiving data as well as
    adjust Arduino clock speed """
    def __init__(self,parent):
        ROVguiBaseClasses.communicationsSettingsDialog.__init__(self,parent)
        
        # set up validators to prevent non-numeric stuff from being entered
        self.arduinoLoopFreqTextControl.SetValidator(IntValidator())
        self.videoFrameFreqTextControl.SetValidator(IntValidator())
        self.controlInputsFreqTextControl.SetValidator(IntValidator())
        self.sensorReadingsFreqTextControl.SetValidator(IntValidator())
        
        # set initial values
        self.arduinoLoopFreqTextControl.SetValue(str(self.GetParent().freqArduino))
        self.videoFrameFreqTextControl.SetValue(str(self.GetParent().freqVideo))
        self.controlInputsFreqTextControl.SetValue(str(self.GetParent().freqControlInputs))
        self.sensorReadingsFreqTextControl.SetValue(str(self.GetParent().freqSensorReadings))
    
    def setArduinoFreq(self,event):
        if self.arduinoLoopFreqTextControl.GetValue():
            self.GetParent().freqArduino = int(self.arduinoLoopFreqTextControl.GetValue())
            self.GetParent().controlParameters['refreshRate'] = int(1000./self.GetParent().freqArduino)
    
    def setVideoFreq(self,event):
        # TODO there should be a built-in way to transfer data, can't find it right now
        if self.videoFrameFreqTextControl.GetValue():
            self.GetParent().freqVideo = int(self.videoFrameFreqTextControl.GetValue())
            self.GetParent().frameTimer.Start(int(1.0/self.GetParent().freqVideo*1000.0))
    
    def setControlFreq(self,event):
        if self.controlInputsFreqTextControl.GetValue():
            self.GetParent().freqControlInputs = int(self.controlInputsFreqTextControl.GetValue())
            self.GetParent().controlInputTimer.Start(int(1.0/self.GetParent().freqControlInputs*1000.0))
    
    def setSensorsFreq(self,event):
        if self.sensorReadingsFreqTextControl.GetValue():
            self.GetParent().freqSensorReadings = int(self.sensorReadingsFreqTextControl.GetValue())
            self.GetParent().sensorReadingsTimer.Start(int(1.0/self.GetParent().freqSensorReadings*1000.0))
    
    def changedFrameDir(self,event):
        self.GetParent().videoDirectory = self.videoFramePathPicker.GetPath()
    
    def closedSettingsDialog(self,even):
        self.Destroy()
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

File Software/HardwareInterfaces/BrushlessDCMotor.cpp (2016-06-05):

#include "BrushlessDCMotor.h"

// Method definitions.
BrushlessDCMotor::BrushlessDCMotor
(
	const char* motorID,
	int maximumThrustValue,
	int maximumEnginePulseWidth,
	int minimumEnginePulseWidth,
	int armEnginePulseWidth,
	int motorPinInput,
	int relayPinInput
)
:
Module(motorID),
currentPulseWidth(0), // Ditto - zero thrust.
maxThrustValue(maximumThrustValue),
maxPulseWidth(maximumEnginePulseWidth),
minPulseWidth(minimumEnginePulseWidth),
armPulseWidth(armEnginePulseWidth),
reversedThrust(false), // By default the thrust isn't reversed.
motorPin(motorPinInput),
relayPin(relayPinInput)
/* BrushlessDCMotor contructor. Initialise all the class fields, do nothing else.
 * 
 * @param motorID - int that is a unique number used to distinguish all the
 * 	motors connected to the Arduino.
 * @param maximumThrustValue - maximum value of the desired thrust that will be
 * 	supplied to this class. Used to scale the desired thrust to the pulse width.
 * @param minPulseWidth,maxPulseWidth - the range of the pusle widths accepted
 * 	by the used electronic speed controller, in microseconds.
 * @param motorPinInput - Arduino pin to which the motor is connected.
 * @param relayPinInput - Arduino pin to which the relay is connected. The relay
 * 	is used to reverse the thrust of the engine.
 */
{
	pinMode(relayPin,OUTPUT); // We will only flick the relay, so it's a simple output pin.
}	

BrushlessDCMotor::BrushlessDCMotor
(
	const char* motorID,
	int motorPinInput,
	int relayPinInput
)
:
Module(motorID),
currentPulseWidth(-1), // Ditto - zero thrust.
maxThrustValue(-1),
maxPulseWidth(-1),
minPulseWidth(-1),
reversedThrust(false), // By default the thrust isn't reversed.
motorPin(motorPinInput),
relayPin(relayPinInput)
/* BrushlessDCMotor contructor. Initialise the class fields corresponding
 * to the motorIndentifier integer, as well as the Arudino pins that the motor
 * and a relay (used to reverse thrust) are connected to. All the remaining 
 * class fields are initialised with invlaid values to make sure errors are
 * thrown when someone uses fields without consciously setting their values
 * using setRelayPin, setMotorPin, setThrustValueRange and setPulseWidthRnage
 * methods (pins should be set before the ranges).
 * 
 * @param motorID - int that is a unique number used to distinguish all the
 * 	motors connected to the Arduino.
 * @param motorPinInput - Arduino pin to which the motor is connected.
 * @param relayPinInput - Arduino pin to which the relay is connected. The relay
 * 	is used to reverse the thrust of the engine.
 */
{
	// Can't attach to a servo yet because we don't know the range of pulse widths; this will be done when arming the motor anyway.
	pinMode(relayPin,OUTPUT); // We will only flick the relay, so it's a simple output pin.
}

BrushlessDCMotor::BrushlessDCMotor()
:
currentPulseWidth(-1), // Zero thrust.
maxThrustValue(-1),
maxPulseWidth(-1),
minPulseWidth(-1),
reversedThrust(false), // By default the thrust isn't reversed.
motorPin(-1),
relayPin(-1)
/* Default contructor, initialise all the class fields with invlaid values to
 * make sure errors are thrown when someone uses fields without consciously
 * setting their values using setRelayPin, setMotorPin, setThrustValueRange and
 * setPulseWidthRnage methods (pins should be set before the ranges).
 */
{
}

void BrushlessDCMotor::setThrustValueRange(int maximumThrustValue)
/* Set the maxThrustValue and minThrustValue class fields that describe the
 * range of the currentValue that will be translated to engine thrust.
 *
 * @param maximumThrustValue - maximum of the thrust values that will be
 * 	provided to this BrushlessDCMotor.
 */
{
	maxThrustValue=maximumThrustValue;
}

void BrushlessDCMotor::setPulseWidthRange(int maximumEnginePulseWidth, int minimumEnginePulseWidth)
/* Set the maxPulseWidth and maxPulseWidth class fields that describe the
 * range of the pulse widths translate to engine thrust (brushless motor's thrust
 * is described by the width of the pulse in the pulse width modulation). These
 * fields are specific to the electronic speed controller (ESC) used to drive
 * the motor.
 *
 * @param maximumEnginePulseWidth,minimumEnginePulseWidth - range of the pulse
 * 	widths that correspond to maximum and minimum RPMs of this motor. In microseconds.
 */
{
	minPulseWidth=minimumEnginePulseWidth;
	maxPulseWidth=maximumEnginePulseWidth;
}

void BrushlessDCMotor::setMotorPin(int motorPinInput)
/* Set the motorPin class field that says which pin on the Arduino the motor is
 * physically connected to. setPulseWidthRange method should be called after
 * this one to create the pulse width modulation interface.
 */
{
	motorPin=motorPinInput;
	// Can't attach the Servo class yet, we don't know the range of pulse widths. This will be handled in setPulseWidthRange method.
}

void BrushlessDCMotor::setRelayPin(int relayPinInput)
/* Set the relayPin class field that says which pin on the Arduino the relay is
 * physically connected to. This relay is used to reverse the thrust of the engine
 * by reversing the direction of the current flow through it. Also set the relayPin
 * as output.
 */
{
	relayPin=relayPinInput;
	pinMode(relayPin,OUTPUT); // We will only flick the relay, so it's a simple output pin.
}

void BrushlessDCMotor::setValue(int newThrust)
/* Set the throttle of the engine to the desired value. This is achieved by setting
 * the width of the pulse on the motorPin to the appropriate value by scaling
 * newThrust, which has to be between 0 and maxThrustValue,
 * to the pulse width, bound by minPulseWidth and maxPulseWidth.
 * 
 * If newThrust is negative, the direction of the thrust will be reversed by
 * reversing the direction of current flow through the motor by using a relay.
 * 
 * @param newThrust - a value between 0 and maxThrustValue that will be
 * 	scaled to the pusle width between minPulseWidth and	maxPulseWidth class
 * 	attributes. newThrust can be negative to indicate reverse thrust direction.
 */
{//TODO: when reversing thrust go through the zero throttle position to avoid burning shit.
	if(newThrust<0){ // < 0, if we set thrust to 0 make sure we're working forward again, it is likely we will go reverse->0->forward.
		reversedThrust=true; // Keep track of the fact we're working backwards.
		digitalWrite(relayPin,HIGH); // Flick the relay.
	}
	else // Go back to normal thrust direction.
	{
		reversedThrust=false;
		digitalWrite(relayPin,LOW);
	}
	
	currentValue=newThrust;
	currentPulseWidth = int( minPulseWidth + abs(currentValue)/double(maxThrustValue) * (maxPulseWidth-minPulseWidth) ); // Scale the desired throttle to pulse width and change to an int, as expected by the Servo class.
	#ifdef DEBUG_PRINTOUT
		Serial.print("    Setting pulse width for motor ");Serial.print(identifier);Serial.print( " to ");Serial.println( String(currentPulseWidth) );
	#endif
	
	motor.writeMicroseconds(currentPulseWidth);
}
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

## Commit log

2015-05-25 Created a basic GUI which captures camera feed using ROV and displays it in real time
2015-08-12 Added a dial that can be used to set and monitor thrust of the engines.
2015-09-05 Completed GUI layout, added serial comms functionality, video feed needs more love
    [master.sch]
2015-09-05 Created a class that handles DC brushless motor interfacing and started to work on the main Arduion ROV code.
2015-09-06 Fixed video display, still need to fix OpenCV crashing at reconnecting the feed
    [ROVgui.py]
2015-09-06 Minor bug fixes in the brushless motor controller; now it's debugged.
    [BrushlessDCMotor.cpp, ROVMain.ino]
2015-09-06 Added calibration of the brushless DC motors.
2015-09-06 Derived the motor class from a base Module class to unify hardware interface code.
2015-09-06 Added a depth sensor class and moved serial initialisation to the base class to keep it all nice and clean.
2015-09-08 Started to periodically send sensor readings over serial.
2015-09-08 Simplified definition of motors to avoid repeating the same declarations of labels etc.
    [ROVMain.ino]
2015-09-16 Wrote an input interpretation routine which should pick up inputs from the Arduino and update sensor readings
2015-09-16 Started to send sensor labels in the messages as required by the comms protocol.
2015-09-17 FInished the communication protocol to receive inputs from the Arduino.
2015-09-17 Took photos pf the example circuit to reverse the brushless engine thrust.
2015-09-19 Now the BrushlessDCMotor works, also tested the thrust direction reversal and it works too.
    [BrushlessDCMotor.cpp, ROVMain.ino]
2015-09-19 Made a generic arm() method in the Module class; this gets called during setup() for every module and each derived class implements its own actions required at start-up
2015-09-25 Removed a redundant folder, split the updateState() method to treat video frame, control inputs, and sensor readings independently
2015-09-25 Minor fix resetting the sensor flag after an update has been sent
    [ROVMain.ino]
2015-09-26 Started to return 0 in the arm method by default to be able to use Module directly for command execution.
2015-09-26 Reset the armModules flag to 0 after the modules are armed.
    [ROVMain.ino]
2015-09-26 Limited when debugging output will be printed to serial not to fill the buffer up.
2015-09-26 Added a script for copying custom Arduino libraries in HardwareInterfaces
2015-09-26 Updated the default refresh rate to 10 Hz to cope with default frequenies of sensor update requests and command inputs.
2015-09-26 First fully-functional iteration - controls the motor via a slider
2015-09-26 Removed duplicate of throttleDial.py
2015-09-26 Linked the rps dials to an update function, added settings for choosing refresh rates of data transfer and Arduino
2015-10-18 Controller inputs are now fully working, GUI has been updated to accept them. Need to figure out a neat way of mapping them to throttles as now each stick is hooked up to a motor directly
2015-10-18 Fixed a minor bug in dialog allowing settings of refresh rates to be changed - it was not re-setting the wxTimers and thus not doing anything at all!
    [ROVgui.py]
2016-05-30 Minor fixes in software, camera now works without lags
2016-06-05 Lots of minor fixes, made sure SW and HW work together; need to add a dedicated LED module to make things tidy
    [ROVMain.ino]
2016-07-10 Added the functionality to arm only one actuator.
2016-07-10 Added a LEDModule that wraps turning the forward LEDs on and off.
2016-07-10 added saving video frames to file on desktop (need to add a way to change dir); added smooth controller input mapping
2016-07-10 added a setting for changing path for frame dump, cleaned up a few bits
2016-07-13 Now sae photos in batches not to block the main thread.
2016-07-13 Changed photo saing to be in a separate process, thread wasn't cuting it - it would raise v4l2 errors (hm)
    [ROVgui.py]
2016-07-13 Fixed errors with LEDModule.
    [LEDModule.cpp, ROVMain.ino]
2016-07-13 Fixed uint and int comparison compile warnings.
    [ROVMain.ino]
2016-08-20 Added layout in the __init__ to make everything nicely distrbuted in sizers. Still get badly distributed GUI at startup, however. Possibly due to too long names of controllers in the dropdown list.
    [ROVgui.py]
2016-08-20 Tweaked the settings for starboard vertical motor to make it work at the same RPM and kck in at the same threshlds as port vertical one.
2016-08-21 Fine-tuned one of the motor ESCs for smooth rpm control
2016-08-21 Fixed some spelling errors in the comments.
    [ROVgui.py]
2016-08-21 Split the controller names into several lines, each with at most a given number of characters. This fixes an issue, where the sizers explode if one controller's name is too long.
    [ROVgui.py]
2016-08-26 Fix to controller selection drop-down to make it render OK
    [ROVgui.py]
2016-08-28 Initial commit of the geometry files of version 1.0
    [30PSIPressureSensor.ipt, ArduinoUno.ipt, CommonGNDVDD.ipt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]
2016-09-03 Updated the GA drawings to have a readable font size and indicate all the parts.
    [ROVassembly_external.idw, ROVassembly_internal.idw]
2016-09-03 Added the layout of the motorControlBoard. Gerbers are readily usable.
    [BrushlessMotorControlBoard.csv]
2016-09-03 Removed Documentation folder due to its obsolecence, put drawings into GUI folder
    [master.sch]
2016-09-03 removed obsolete accelerometer interface file
2016-09-03 More fixes in the comments
    [ROVMain.ino]
2016-09-03 Added block diagrams of the Arduino software.
2016-09-03 updated pdf drawings in CAD
